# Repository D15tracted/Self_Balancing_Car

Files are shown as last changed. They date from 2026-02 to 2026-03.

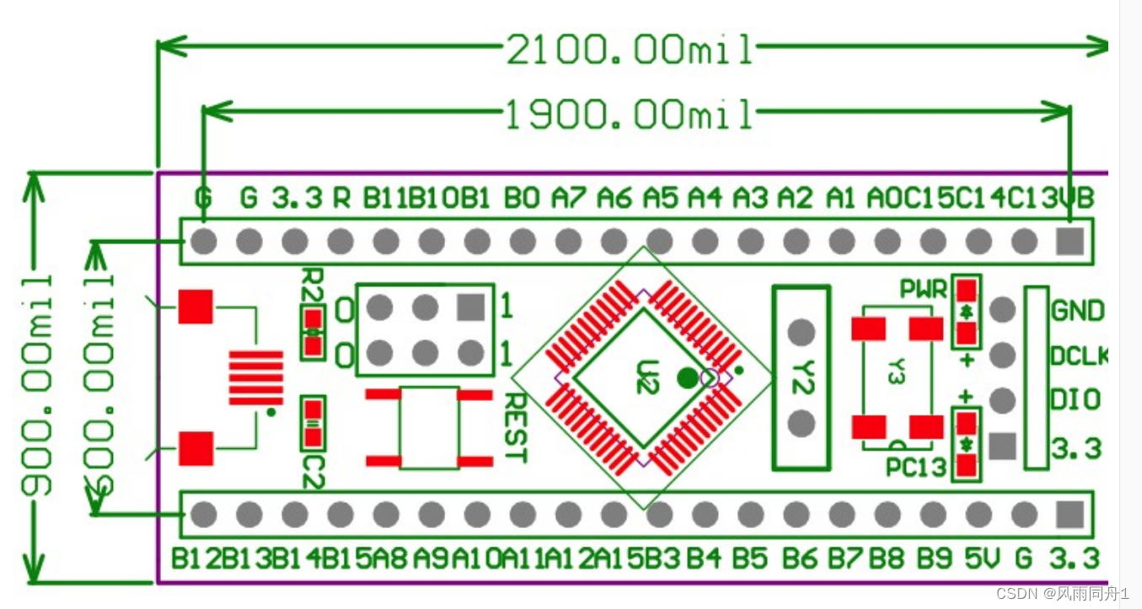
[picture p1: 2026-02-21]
Hardware/Datasheet/STM32F103C8T6_size.png

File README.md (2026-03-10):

# Self_Balancing_Car
This is a project based on tutorials from Bilibili, it have different mechanical stucture and controw board, it use a dm3519 brushless motor instead of a brush motor

related libaries: https://jiangxiekeji.com/download.html
                  https://gitee.com/kit-miao/damiao

Updates:
2026/3/10 implement HAL library

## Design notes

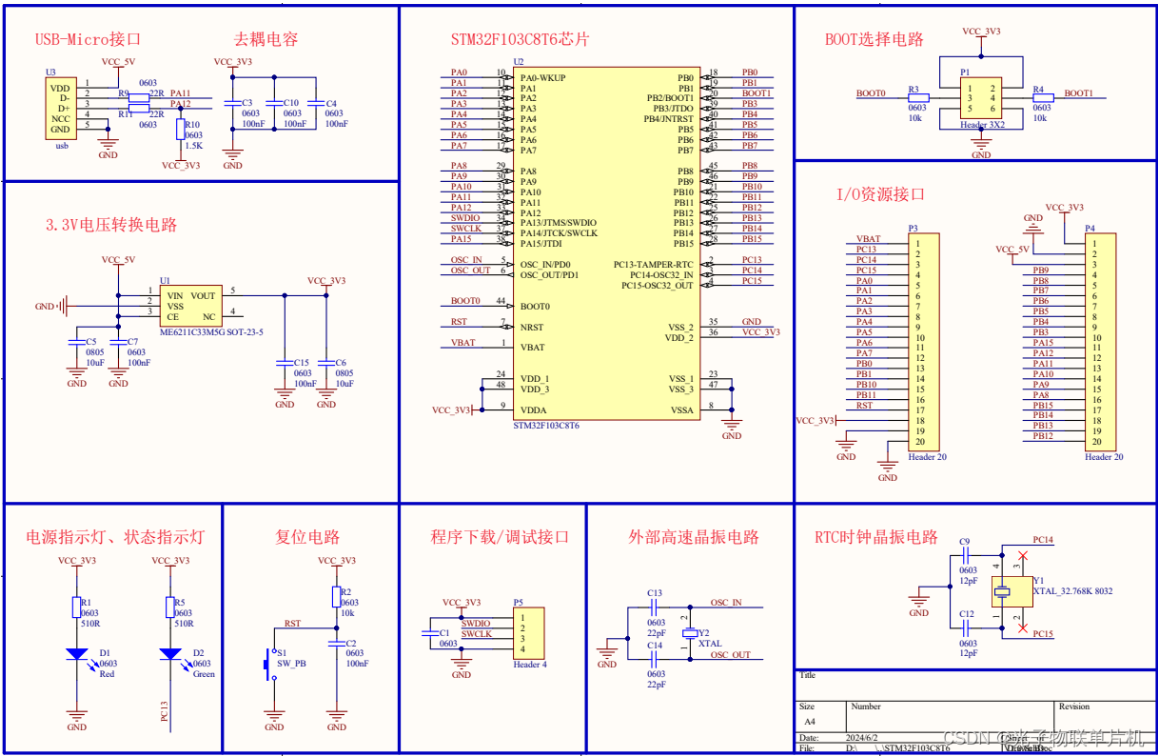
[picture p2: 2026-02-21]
Hardware/Datasheet/STM32F103C8T6_sch.png

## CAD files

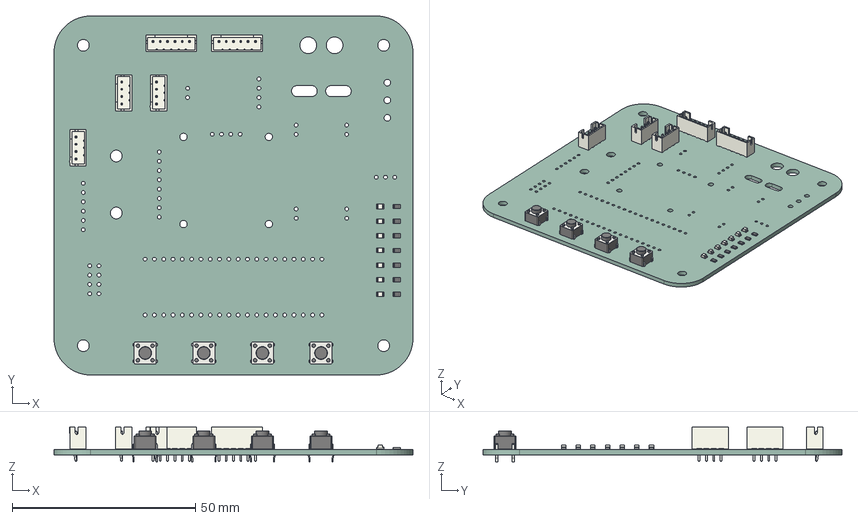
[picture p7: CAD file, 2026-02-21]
Hardware/Self_Balancing_Car.step
98.0 x 98.0 x 9.50 mm
R_0805_2012Metric x 7
LED_0805_2012Metric x 7
SW_PUSH_6mm_H5mm x 4
JST_PH_B6B-PH-K_1x06_P2.00mm_Vertical x 2
JST_PH_B4B-PH-K_1x04_P2.00mm_Vertical x 3
Self_Balancing_Car_PCB

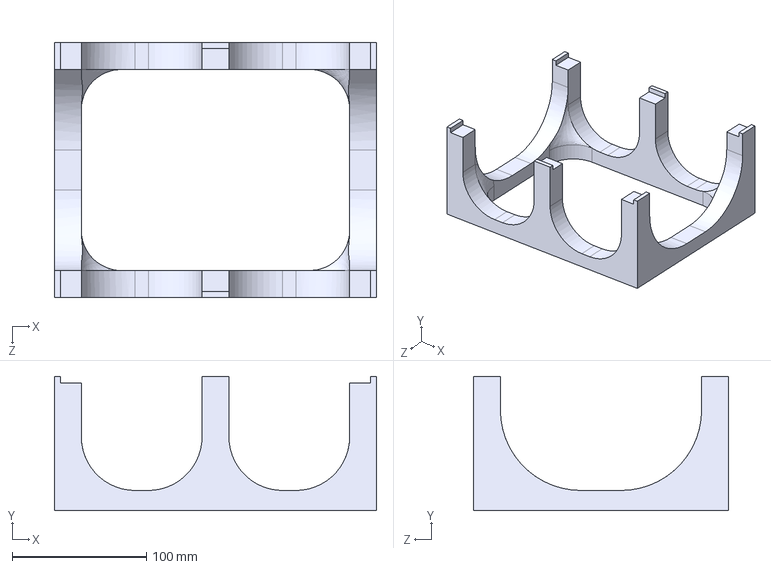
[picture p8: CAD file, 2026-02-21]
Mechanical/!Manufacture/3DP/Rack.STEP
240.0 x 100.0 x 190.0 mm

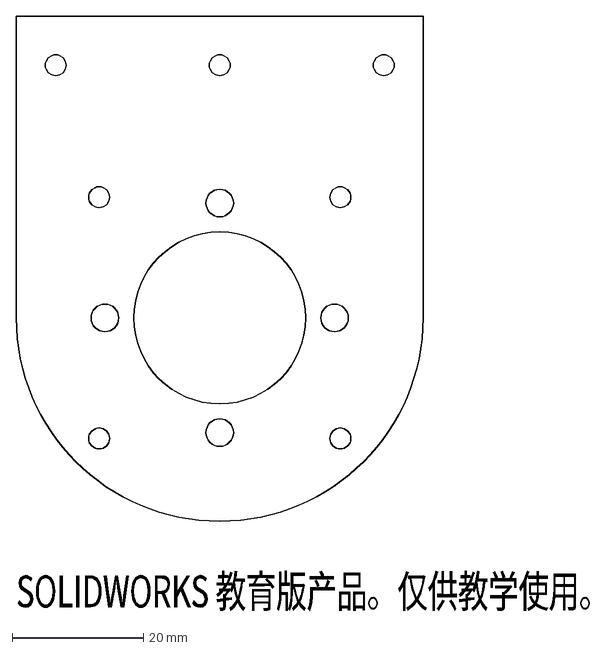
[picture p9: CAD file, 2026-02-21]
Mechanical/!Manufacture/CFP/SBC_CFP03.DXF
SOLIDWORKS 教育版产品。仅供教学使用。

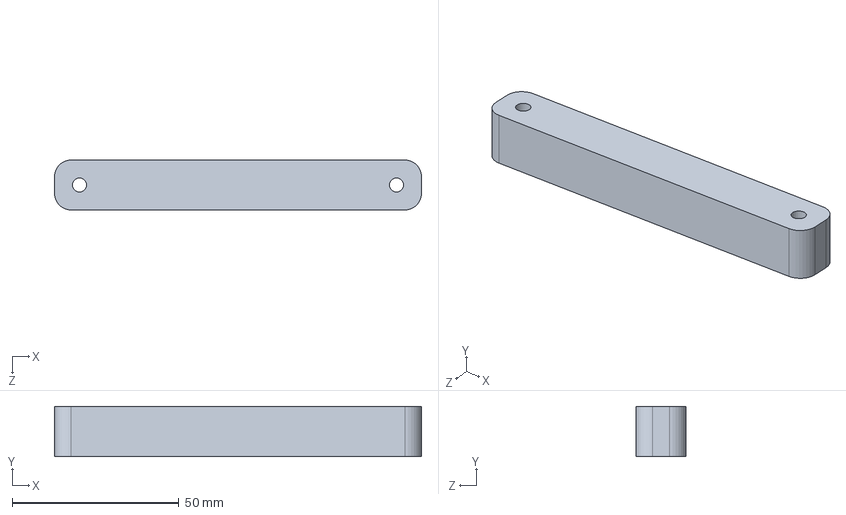
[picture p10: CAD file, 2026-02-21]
Mechanical/3DP/SBC_3DP05.SLDPRT
110.0 x 15.0 x 15.0 mm

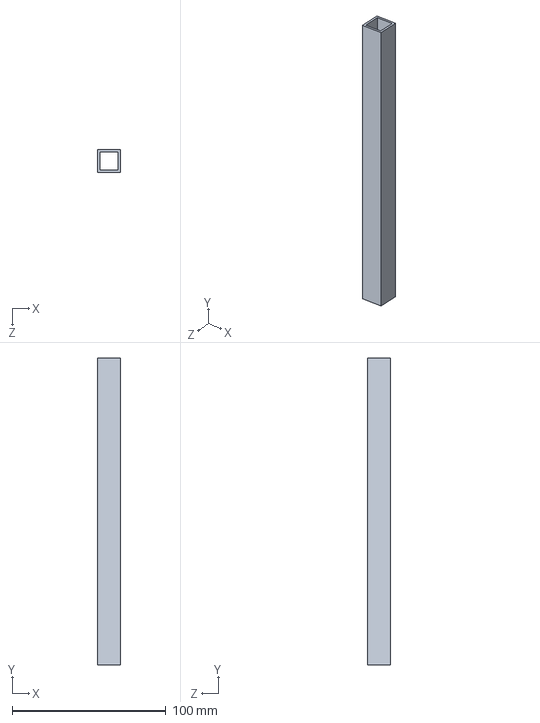
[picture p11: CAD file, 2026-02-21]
Mechanical/Altube/SBC_Altube01.SLDPRT
15.0 x 200.0 x 15.0 mm

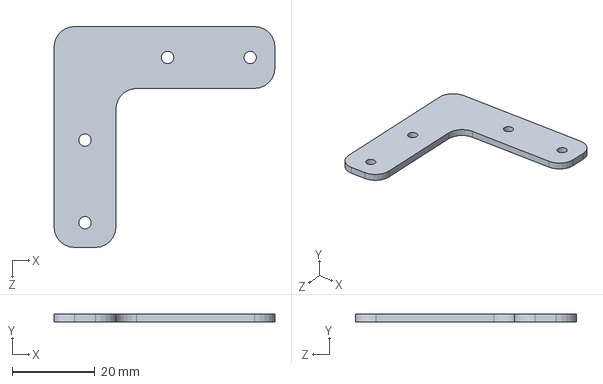
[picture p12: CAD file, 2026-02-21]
Mechanical/CFP/Template90LShape(15mm).SLDPRT
53.5 x 2.00 x 53.5 mm

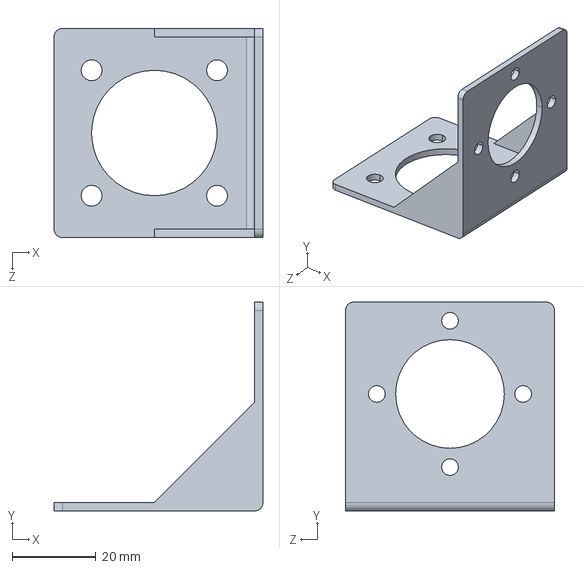
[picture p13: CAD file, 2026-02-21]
Mechanical/Misc/3508电机座.SLDPRT
50.0 x 50.0 x 50.0 mm

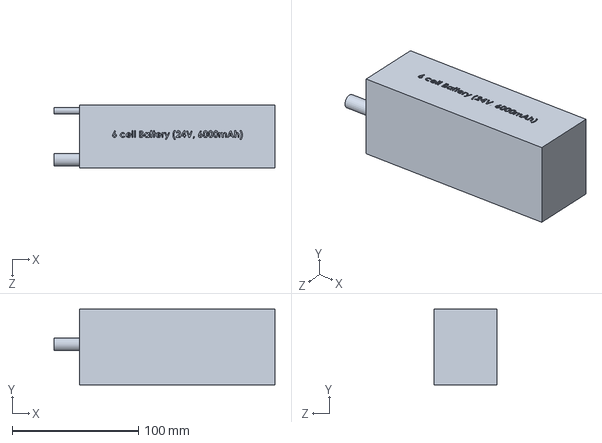
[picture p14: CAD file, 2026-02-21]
Hardware/6 cell battery (24V, 6000mAh).SLDPRT
175.0 x 60.0 x 50.0 mm

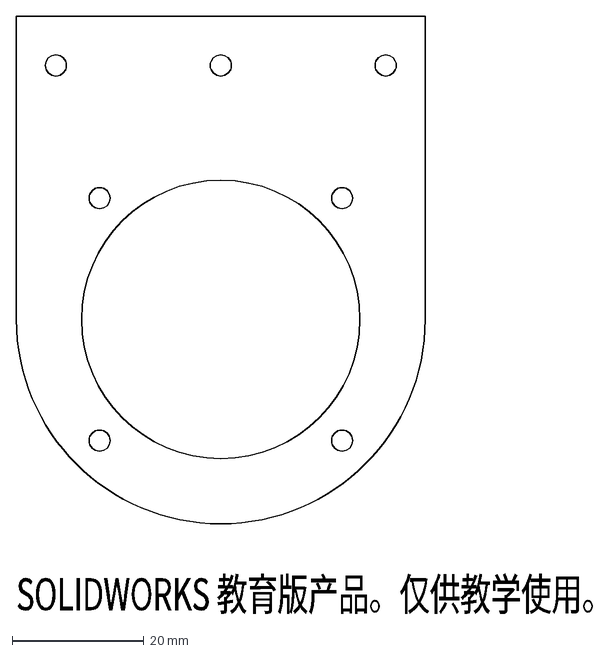
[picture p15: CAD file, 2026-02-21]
Mechanical/!Manufacture/CFP/SBC_CFP04.DXF
SOLIDWORKS 教育版产品。仅供教学使用。

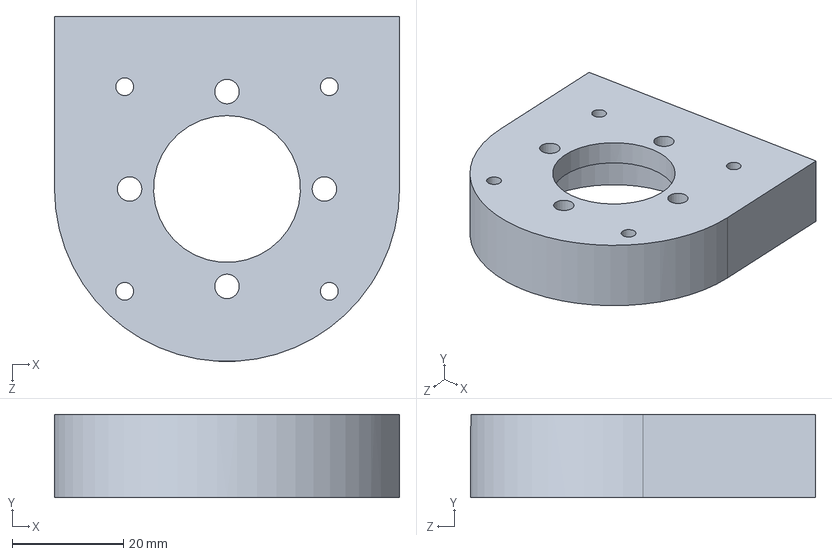
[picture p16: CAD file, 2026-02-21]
Mechanical/3DP/SBC_3DP01.SLDPRT
62.0 x 15.0 x 62.0 mm

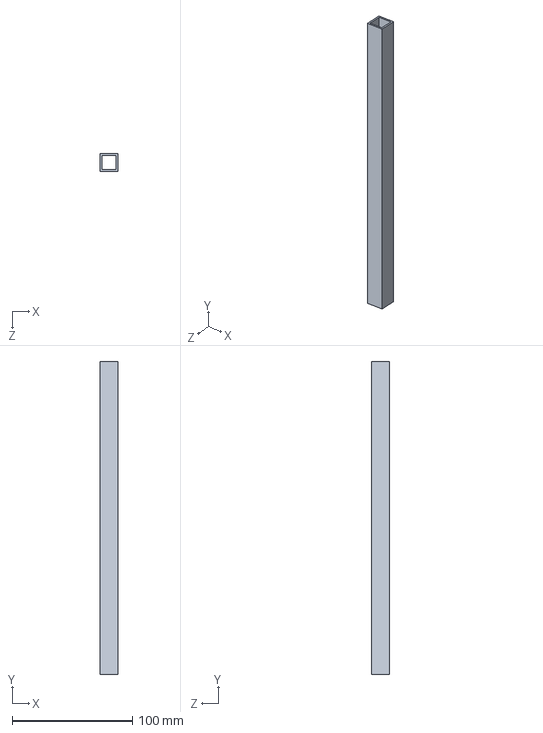
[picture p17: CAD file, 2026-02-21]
Mechanical/Altube/SBC_Altube02.SLDPRT
15.0 x 260.0 x 15.0 mm

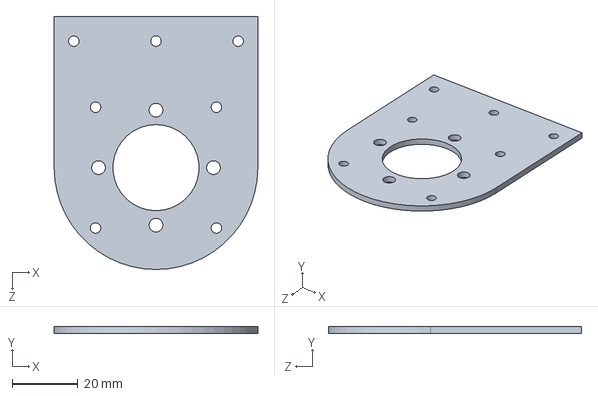
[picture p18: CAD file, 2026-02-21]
Mechanical/CFP/SBC_CFP03.SLDPRT
62.0 x 2.00 x 77.0 mm

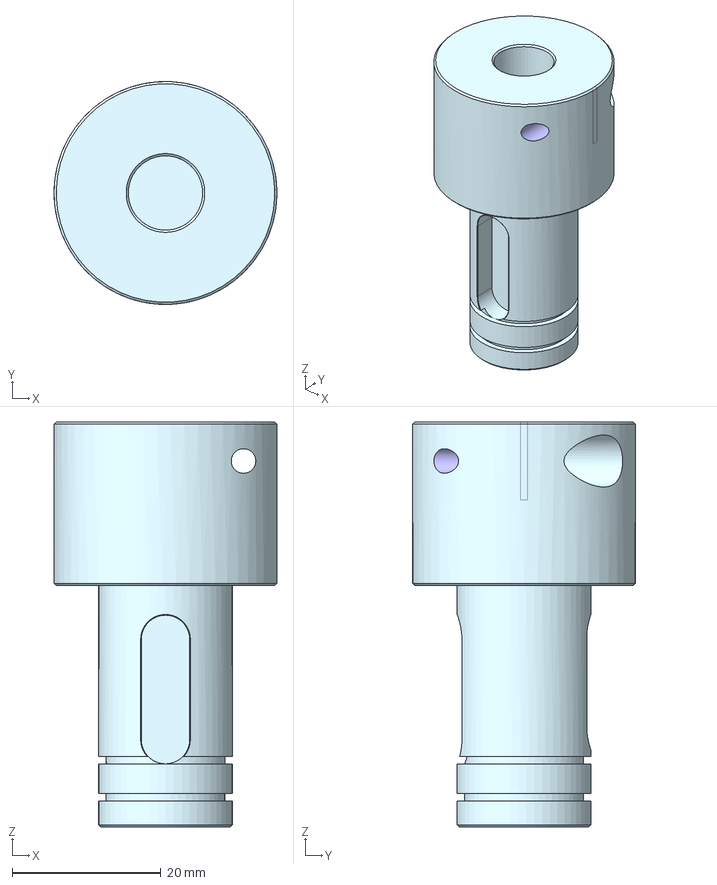
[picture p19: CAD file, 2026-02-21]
Mechanical/Misc/轴直径10mm-抱紧式联轴器-承重轮专用.stp
30.0 x 30.0 x 54.5 mm

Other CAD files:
Mechanical/Rack.SLDPRT
Mechanical/!Manufacture/3DP/SBC_3DP05.STEP
Mechanical/Hardware/SBC_board.SLDPRT
Hardware/SBC_board.SLDPRT
Hardware/3 cell battery (12V, 5200mAh).SLDPRT
Mechanical/!Manufacture/3DP/Rack.3mf
Mechanical/!Manufacture/3DP/SBC_3DP01.3mf
Mechanical/!Manufacture/3DP/SBC_3DP01.STEP
Mechanical/!Manufacture/3DP/SBC_3DP02.STEP
Mechanical/!Manufacture/3DP/SBC_3DP03.3mf
Mechanical/!Manufacture/3DP/SBC_3DP03.STEP
Mechanical/!Manufacture/3DP/SBC_3DP04.STEP
Mechanical/!Manufacture/3DP/SBC_3DP05.3mf
Mechanical/!Manufacture/Altube/SBC_Altube.SLDDRW
Mechanical/!Manufacture/CFP/SBC_CFP01.DXF
Mechanical/!Manufacture/CFP/SBC_CFP02.DXF
Mechanical/!Manufacture/CFP/SBC_CFP05.DXF
Mechanical/!Manufacture/CFP/Template90LShape(15mm).DXF
Mechanical/!Manufacture/CFP/Template90TShape(15mm).DXF
Mechanical/3DP/SBC_3DP02.SLDPRT
Mechanical/3DP/SBC_3DP03.SLDPRT
Mechanical/3DP/SBC_3DP04.SLDPRT
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

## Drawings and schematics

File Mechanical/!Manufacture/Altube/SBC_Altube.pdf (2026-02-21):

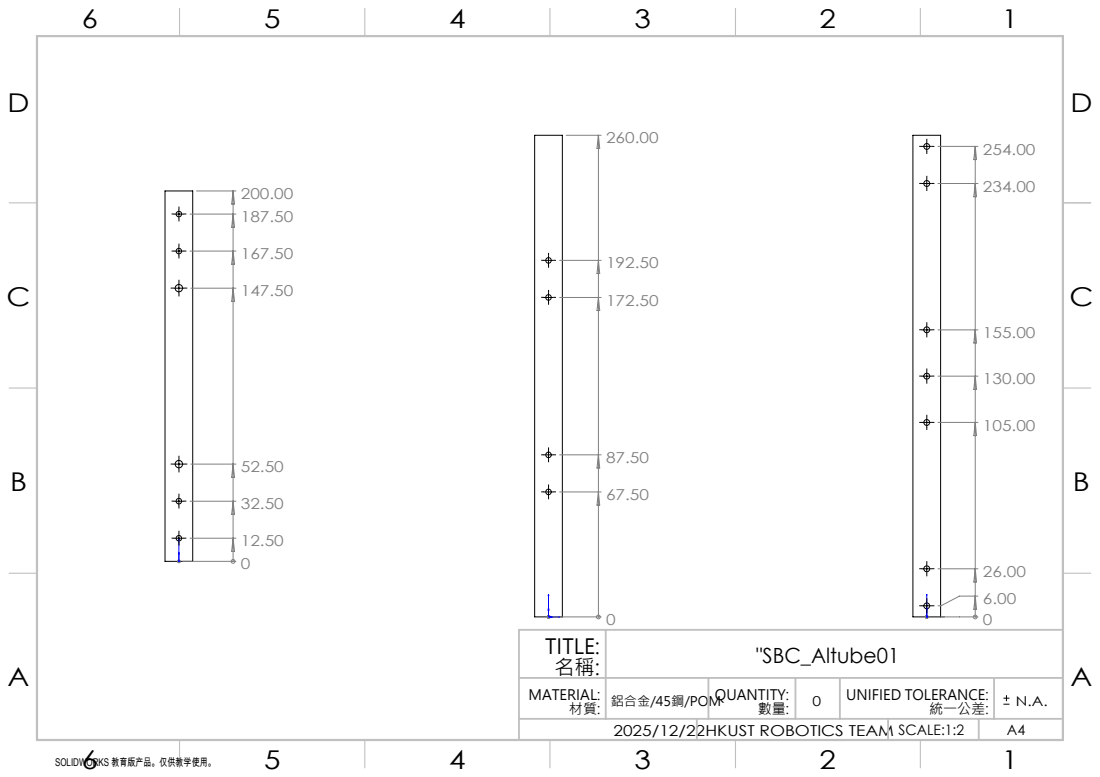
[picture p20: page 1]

TITLE: 名稱: | "SBC_Altube01

MATERIAL: 材質: | | QUANTITY: 數量: | 0 | UNIFIED TOLERANCE: 統一公差:

2025/12/22 | HKUST ROBOTICS TEAM | SCALE:1:2 | A4

SOLIDWORKS 教育版产品。仅供教学使用。

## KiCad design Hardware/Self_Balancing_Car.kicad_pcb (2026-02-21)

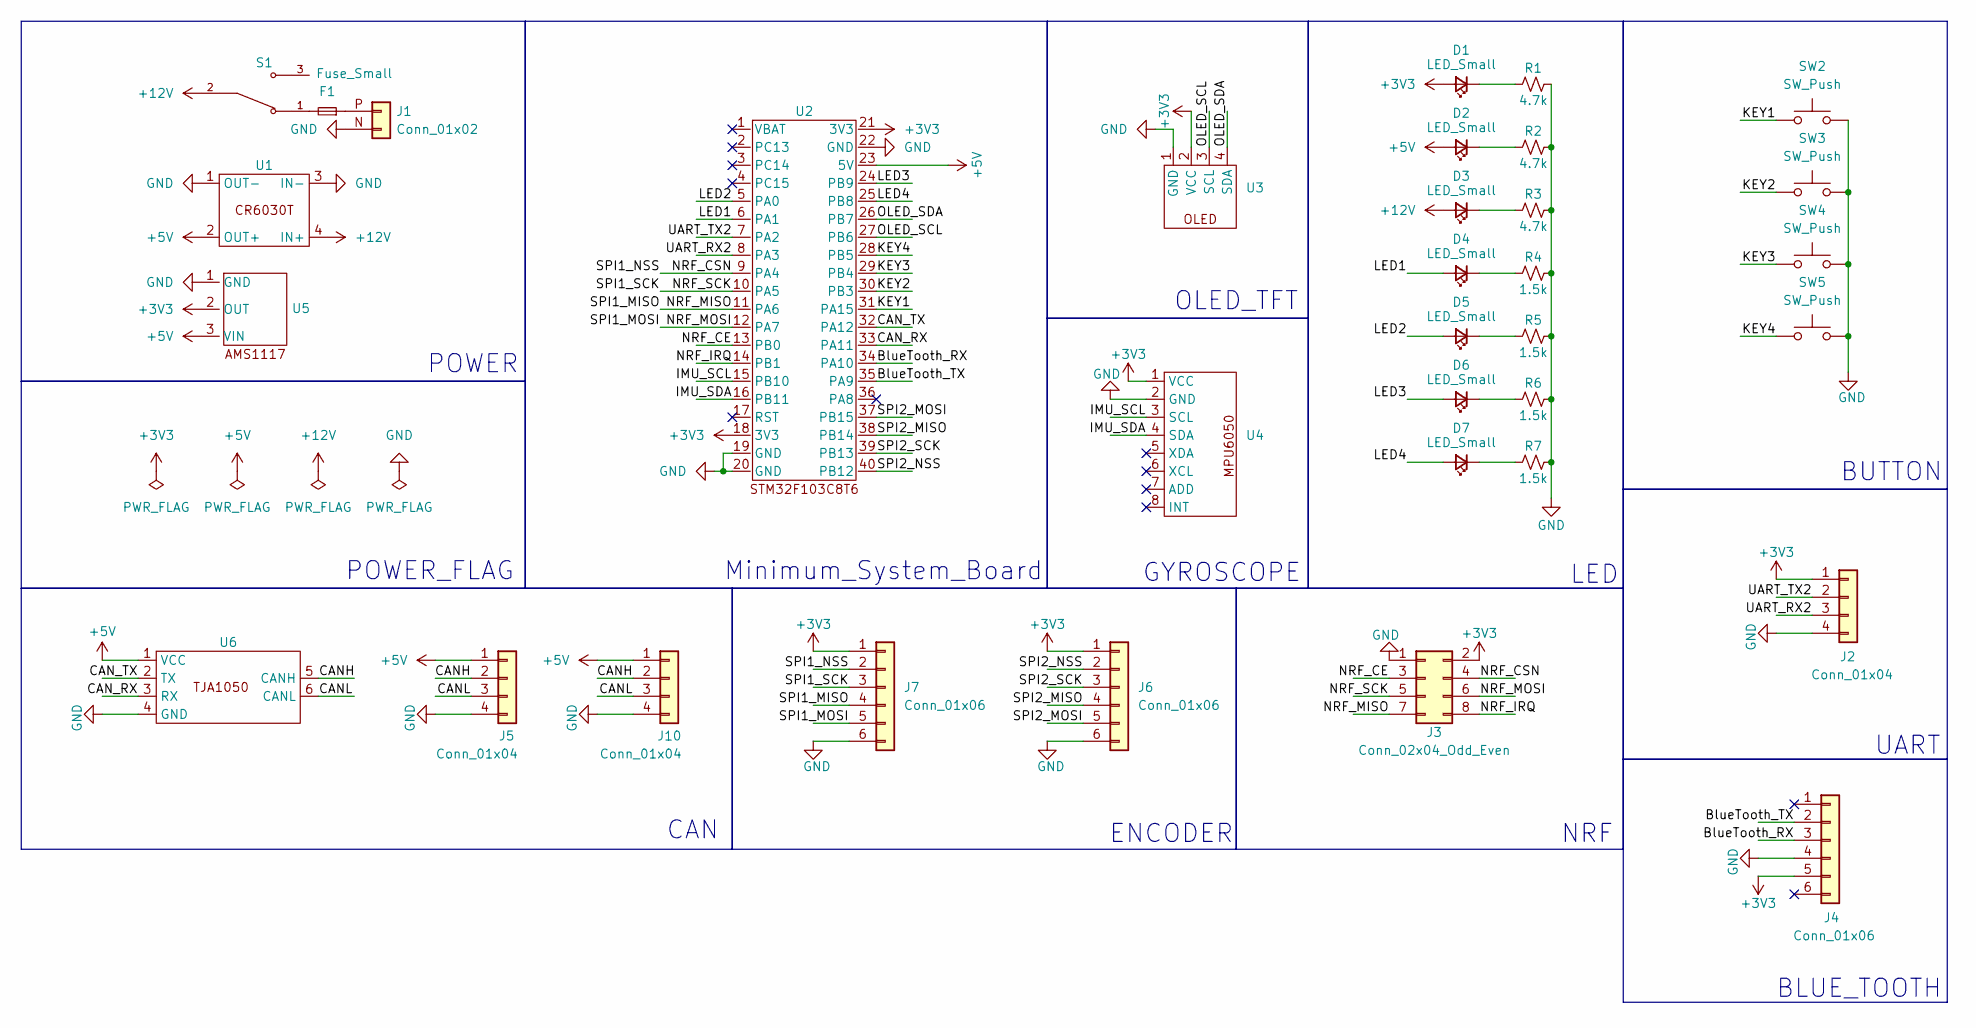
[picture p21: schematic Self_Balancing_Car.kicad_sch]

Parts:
D1, D2, D3, D4, D5, D6, D7: LED_Small; LED_0805_2012Metric
F1: Fuse_Small; Fuse_Blade_ATO_directSolder
J1: Conn_01x02; AMASS_XT60-M
J2, J5, J10: Conn_01x04; JST_PH_B4B-PH-K_1x04_P2.00mm_Vertical
J3: Conn_02x04_Odd_Even; NRF24L01
J4: Conn_01x06; BLUE_TOOTH
J6, J7: Conn_01x06; JST_PH_B6B-PH-K_1x06_P2.00mm_Vertical
R1, R2, R3: 4.7k; R_0805_2012Metric
R4, R5, R6, R7: 1.5k; R_0805_2012Metric
S1: SS12D10
SW2, SW3, SW4, SW5: SW_Push; KEY6x6
U1: CR6030T
U2: STM32F103C8T6_Minimum_System_Board
U3: OLED
U4: MPU6050
U5: AMS1117_Vertical
U6: TJA1050

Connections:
+3V3: D1.2 (A), J2.1, J3.2, J4.5, J6.1, J7.1, U2.18 (3V3), U2.21 (3V3), U3.2 (VCC), U4.1 (VCC), U5.2 (OUT)
+5V: D2.2 (A), J5.1, J10.1, U1.2 (OUT+), U2.23 (5V), U5.3 (VIN), U6.1 (VCC)
+12V: D3.2 (A), S1.2, U1.4 (IN+)
/BlueTooth_RX: J4.3, U2.34 (PA10)
/BlueTooth_TX: J4.2, U2.35 (PA9)
/CANH: J5.2, J10.2, U6.5 (CANH)
/CANL: J5.3, J10.3, U6.6 (CANL)
/CAN_RX: U2.33 (PA11), U6.3 (RX)
/CAN_TX: U2.32 (PA12), U6.2 (TX)
/IMU_SCL: U2.15 (PB10), U4.3 (SCL)
/IMU_SDA: U2.16 (PB11), U4.4 (SDA)
/KEY1: SW2.1, U2.31 (PA15)
/KEY2: SW3.1, U2.30 (PB3)
/KEY3: SW4.1, U2.29 (PB4)
/KEY4: SW5.1, U2.28 (PB5)
/LED1: D4.2 (A), U2.6 (PA1)
/LED2: D5.2 (A), U2.5 (PA0)
/LED3: D6.2 (A), U2.24 (PB9)
/LED4: D7.2 (A), U2.25 (PB8)
/NRF_CE: J3.3, U2.13 (PB0)
/NRF_CSN: J3.4, J7.2, U2.9 (PA4)
/NRF_IRQ: J3.8, U2.14 (PB1)
/NRF_MISO: J3.7, J7.4, U2.11 (PA6)
/NRF_MOSI: J3.6, J7.5, U2.12 (PA7)
/NRF_SCK: J3.5, J7.3, U2.10 (PA5)
/OLED_SCL: U2.27 (PB6), U3.3 (SCL)
/OLED_SDA: U2.26 (PB7), U3.4 (SDA)
/SPI2_MISO: J6.4, U2.38 (PB14)
/SPI2_MOSI: J6.5, U2.37 (PB15)
/SPI2_NSS: J6.2, U2.40 (PB12)
/SPI2_SCK: J6.3, U2.39 (PB13)
/UART_RX2: J2.3, U2.8 (PA3)
/UART_TX2: J2.2, U2.7 (PA2)
GND: J1.N (Pin_2), J2.4, J3.1, J4.4, J5.4, J6.6, J7.6, J10.4, R1.2, R2.2, R3.2, R4.2, R5.2, R6.2, R7.2, SW2.2, SW3.2, SW4.2, SW5.2, U1.1 (OUT-), U1.3 (IN-), U2.19 (GND), U2.20 (GND), U2.22 (GND), U3.1 (GND), U4.2 (GND), U5.1 (GND), U6.4 (GND)
unnamed: D1.1 (K), R1.1
unnamed: D2.1 (K), R2.1
unnamed: D3.1 (K), R3.1
unnamed: D4.1 (K), R4.1
unnamed: D5.1 (K), R5.1
unnamed: D6.1 (K), R6.1
unnamed: D7.1 (K), R7.1
unnamed: F1.2, S1.1
unnamed: F1.1, J1.P (Pin_1)

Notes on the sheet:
BUTTON
Minimum_System_Board
LED
ENCODER
POWER
NRF
GYROSCOPE
UART
POWER_FLAG
OLED_TFT
CAN
BLUE_TOOTH

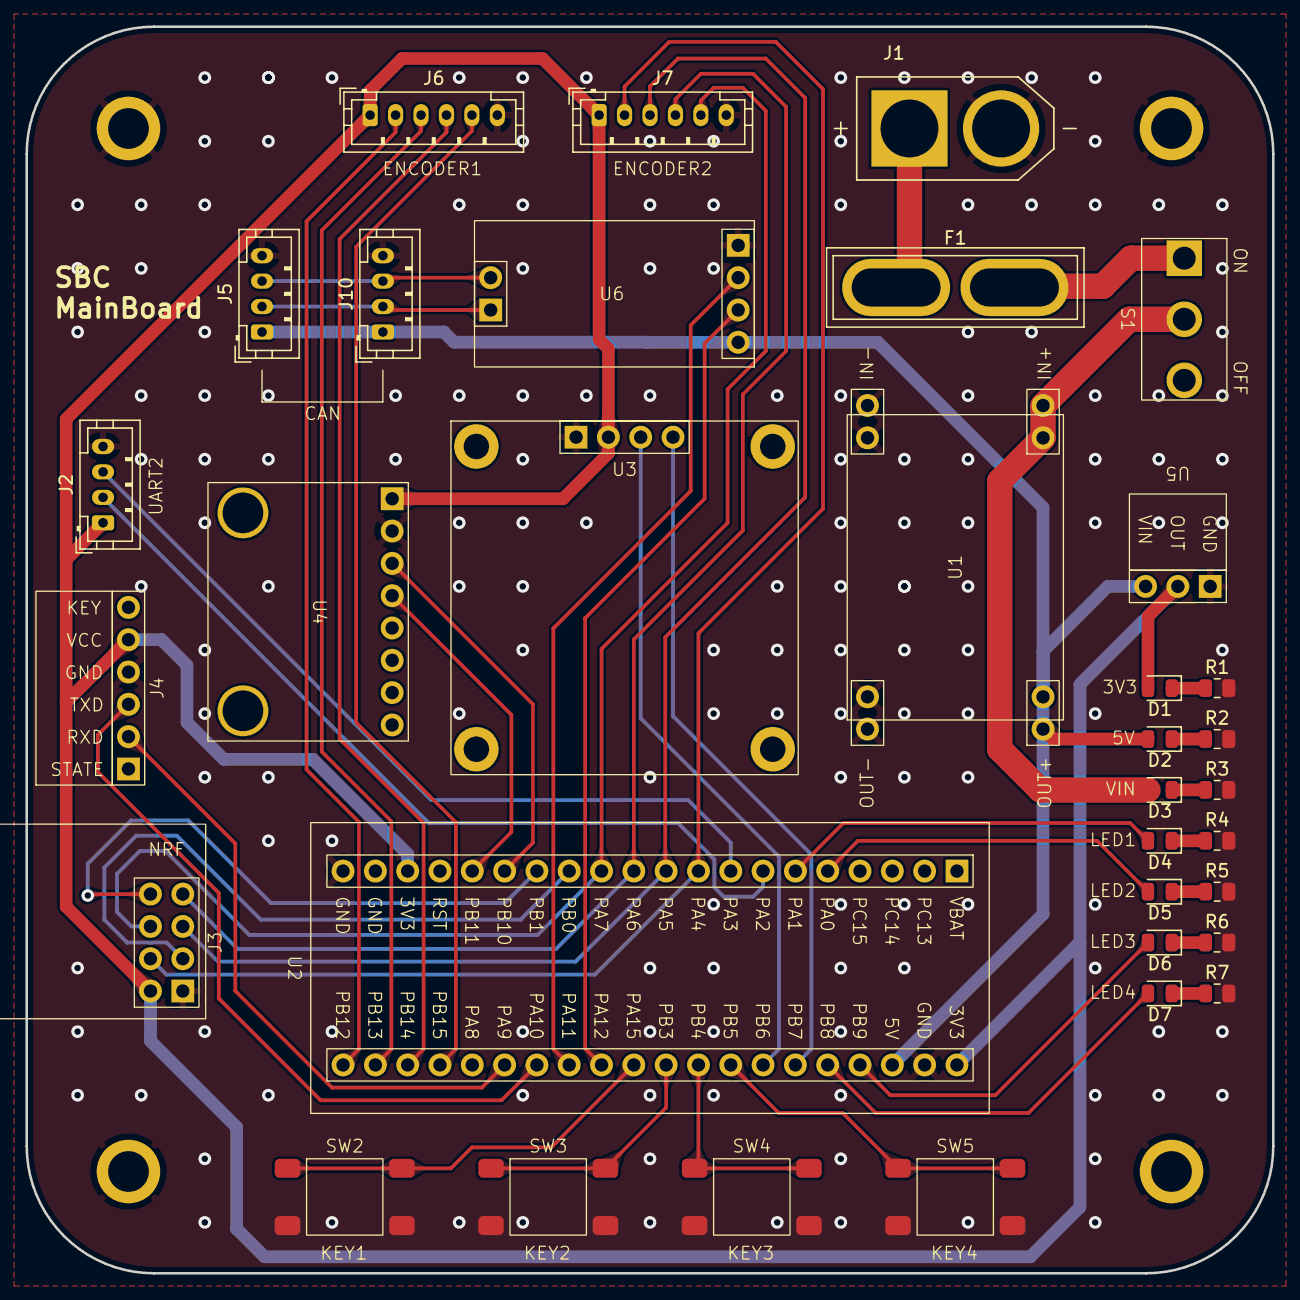
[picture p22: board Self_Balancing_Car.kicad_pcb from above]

Board: 2 copper layers, 98.0 x 98.0 mm, 34 parts (0 on the bottom side), 43 nets.

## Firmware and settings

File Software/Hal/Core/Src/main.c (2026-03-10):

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
/* Includes ------------------------------------------------------------------*/
#include "main.h"
#include "can.h"
#include "tim.h"
#include "usart.h"
#include "gpio.h"

/* USER CODE BEGIN Includes */
#include "OLED.h"
#include "MPU6050.h"
#include "Serial.h"
#include "Control.h"
#include "LED.h"
#include "KEY.h"
#include "MyCAN.h"
#include "dm_motor_ctrl.h"
#include "dm_motor_drv.h"
#include "PID.h"
#include <math.h>
#include <string.h>
#include <stdlib.h>

/* USER CODE END Includes */


/* USER CODE BEGIN PV */
uint8_t RunFlag;

int plotnum = 0;

float data[5] = {0,0,0,0,0};

float LmPos = 0;
float LmVel = 0;
float LmKp = 0;
float LmKd = 5;
float LmTor = 0;

float RmPos = 0;
float RmVel = 0;
float RmKp = 0;
float RmKd = 5;
float RmTor = 0;

float AngleActual2 = 0;

float SpeedActual2 = 0;

float TurnActual2 = 0;

float LeftSpeed1 = 0;

float RightSpeed1 = 0;

motor_t *m1;
motor_t *m2;

float AveVel, DifVel;

float LeftSpeed, RightSpeed;
float LeftSpeedFiltered, RightSpeedFiltered;
float AveSpeed;

uint32_t RxID;
uint8_t RxLength;
uint8_t RxData[8];

int16_t AX, AY, AZ, GX, GY, GZ;
uint8_t TimerErrorFlag;
uint16_t TimerCount;

float AngleAcc;
float AngleGyro;
float Angle;

PID_t AnglePID = {
	.Kp = 0.2, //0.2
	.Ki = 0.03,  //0.03
	.Kd = 0.1,  //0.1
	
	.OutMax = 100,
	.OutMin = -100,
	
	.OutOffset = 0,
	
	.ErrorDecayFactor = 1,
	.ErrorIntMax = 400,
	.ErrorIntMin = -400,
};

PID_t SpeedPID = {
	.Kp = 0.8,  //0.8
	.Ki = 0.1,  //0.1
	.Kd = 0.5,  //0.5
	
	.OutMax = 7,
	.OutMin = -7,
	
	.ErrorDecayFactor = 3,
	.ErrorIntMax = 50,
	.ErrorIntMin = -50,
};

static uint16_t Count0 = 0, Count1 = 0, Count2 = 0;
/* USER CODE END PV */

void SystemClock_Config(void);
/**
  * @brief  The application entry point.
  * @retval int
  */
int main(void)
{

  /* MCU Configuration--------------------------------------------------------*/

  /* Reset of all peripherals, Initializes the Flash interface and the Systick. */
  HAL_Init();

  /* USER CODE BEGIN Init */
	__HAL_AFIO_REMAP_SWJ_NOJTAG();
  /* USER CODE END Init */

  /* Configure the system clock */
  SystemClock_Config();

  /* Initialize all configured peripherals */
  MX_GPIO_Init();
  MX_CAN_Init();
  MX_USART1_UART_Init();
  MX_TIM1_Init();
  /* USER CODE BEGIN 2 */
	OLED_Init();
	MPU6050_Init();
	Serial_Init();
	MyCAN_Init();
	dm_motor_init();
	HAL_TIM_Base_Start_IT(&htim1);
	
	m1 = &motor[Motor1];
	m1->id = 0x01;
	m1->ctrl.mode = mit_mode;
	m1->para.pos = 0;
	m1->para.vel = 0;
	m1->para.tor = 0;
	
	m2 = &motor[Motor2];
	m2->id = 0x02;
	m2->ctrl.mode = mit_mode;
	m2->para.pos = 0;
	m2->para.vel = 0;
	m2->para.tor = 0;
  /* USER CODE END 2 */

  /* Infinite loop */
  /* USER CODE BEGIN WHILE */
  while (1)
  {
		if (RunFlag) {
		dm_motor_enable(m1);
		dm_motor_enable(m2);
		} 
		else {
		dm_motor_disable(m1);
		dm_motor_disable(m2);
		}
		
		if (RunFlag) {LED1_ON();} else {LED1_OFF();}
		
		if (Key_Check(KEY_1, KEY_DOWN))
		{
			if (RunFlag == 0)
			{
				PID_Init(&AnglePID);
				PID_Init(&SpeedPID);
				RunFlag = 1;
			}
			else
			{
				RunFlag = 0;
			}
		}
		
		OLED_Clear();
		
		if (Serial_RxFlag == 1){
			Control_Rx(data);
		}
		
		if(data[0] == 2){
				SpeedPID.Target = data[2] / 20.0;
				DifVel = -data[3] / 50.0;
		}
		
		if(data[0] == 2){
			if(fabsf(data[1]) > 95 || fabsf(data[4]) > 95){
				RunFlag = 0;
			}
		}
		
		if(data[0] == 3) {plotnum = data[1];}
		
		if(plotnum != 0){
			if(plotnum == 1){
				printf("[plot,%f,%f]", m1->para.pos, m2->para.pos);
			}
			if(plotnum == 2){
				printf("[plot,%f,%f]", m1->para.vel, m2->para.vel);
			}
			if(plotnum == 3){
				printf("[plot,%f,%f]", m1->para.tor, m2->para.tor);
			}
			if(plotnum == 4){
				printf("[plot,%f,%f,%f]", AngleAcc, AngleGyro, Angle);
			}
			if(plotnum == 5){
				printf("[plot,%f,%f,%f,%f,%f]", AnglePID.Kp * AnglePID.Error0, AnglePID.Ki * AnglePID.ErrorInt, AnglePID.Kd * AngleActual2, AnglePID.Target, AnglePID.Actual);
			}
			if(plotnum == 6){
				printf("[plot,%f,%f,%f,%f,%f]", SpeedPID.Kp * SpeedPID.Error0, SpeedPID.Ki * SpeedPID.ErrorInt, SpeedPID.Kd * SpeedActual2, SpeedPID.Target, SpeedPID.Actual);
			}
		}
		
		OLED_Printf(0, 0, OLED_6X8, "P:%05.2fr", m1->para.pos);
		OLED_Printf(0, 8, OLED_6X8, "V:%05.2fr/s", m1->para.vel);
		OLED_Printf(0, 16, OLED_6X8, "T:%05.2fNm", m1->para.tor);
		
		OLED_Printf(0, 32, OLED_6X8, "P:%05.2fr", m2->para.pos);
		OLED_Printf(0, 40, OLED_6X8, "V:%05.2fr/s", m2->para.vel);
		OLED_Printf(0, 48, OLED_6X8, "T:%05.2fNm", m2->para.tor);
		
		OLED_Printf(64, 0, OLED_6X8, "Aa:%05.2f", AngleAcc);
		OLED_Printf(64, 8, OLED_6X8, "Ag:%05.2f", AngleGyro);
		OLED_Printf(64, 16, OLED_6X8, "Af:%05.2f", Angle);
		
		OLED_Printf(64, 32, OLED_6X8, "%05d", AX);
		OLED_Printf(64, 40, OLED_6X8, "%05d",	AY);
		OLED_Printf(64, 48, OLED_6X8, "%05d", AZ);
		OLED_Printf(96, 32, OLED_6X8, "%05d", GX);
		OLED_Printf(96, 40, OLED_6X8, "%05d", GY);
		OLED_Printf(96, 48, OLED_6X8, "%05d", GZ);
		
		OLED_Printf(0, 56, OLED_6X8, "%01d", Serial_RxFlag);
		OLED_Printf(64, 56, OLED_6X8, "%02.2f", SpeedPID.Target);
		OLED_Printf(96, 56, OLED_6X8, "%02.2f", DifVel);

		OLED_Update();
    /* USER CODE END WHILE */

    /* USER CODE BEGIN 3 */
  }
  /* USER CODE END 3 */
}

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
/* USER CODE BEGIN 4 */
void HAL_TIM_PeriodElapsedCallback(TIM_HandleTypeDef *htim)
{
    if (htim->Instance == TIM1)
    {
        // 按键扫描（若 Key 模块依赖定时器）
        Key_Tick();   // 需确认 Key 模块是否已移植

        // 串口接收超时检测（Count2 逻辑）
        Count2++;
        if (Serial_RxFlag == 1) {
            Count2 = 0;
        }
        if (Count2 >= 500) {
            Count2 = 0;
            data[0] = 0; data[1] = 0; data[2] = 0; data[3] = 0; data[4] = 0;
            SpeedPID.Target = 0;
            DifVel = 0;
        }

        // 每 10ms 执行一次（假设定时器周期 1ms）
        Count0++;
        if (Count0 >= 10) {
            Count0 = 0;

            // 读取 MPU6050
            MPU6050_GetData(&AX, &AY, &AZ, &GX, &GY, &GZ);

            // 数据校准（根据原代码）
            GY = -GY;
            GY -= 114;
            AX = -AX;
            AZ = -AZ;

            // 角度计算
            AngleAcc = atan2(AX, AZ) / 3.14159f * 180.0f;
            AngleAcc += 3.55f;
            AngleGyro = Angle + (GY / 32768.0f * 2000.0f * 0.01f);
            float Alpha = 0.003f;
            Angle = Alpha * AngleAcc + (1.0f - Alpha) * AngleGyro;

            // 角度超限保护
            if (Angle > 15.0f || Angle < -15.0f) {
                RunFlag = 0;
            }

            // 电机控制输出
            if (RunFlag) {
                AnglePID.Actual = Angle;
                AngleActual2 = AnglePID.Actual - AnglePID.Actual1;
                PID_Update(&AnglePID);
                AveVel = -AnglePID.Out;

                LmVel = AveVel + DifVel / 2.0f;
                RmVel = AveVel - DifVel / 2.0f;

                // 限幅
                if (LmVel > 10.0f) LmVel = 10.0f;
                else if (LmVel < -10.0f) LmVel = -10.0f;
                if (RmVel > 10.0f) RmVel = 10.0f;
                else if (RmVel < -10.0f) RmVel = -10.0f;

                // 发送 MIT 控制命令
                mit_ctrl(m1, 0x01, LmPos, LmVel, LmKp, LmKd, LmTor);
                mit_ctrl(m2, 0x02, RmPos, -RmVel, RmKp, RmKd, RmTor);
            } else {
                // 停机
                mit_ctrl(m1, 0x01, 0, 0, 0, 0, 0);
                mit_ctrl(m2, 0x02, 0, 0, 0, 0, 0);
            }
        }

        // 每 10ms 读取电机反馈
        Count1++;
        if (Count1 >= 10) {
            Count1 = 0;

            // 发送读取命令
            read_motor_ctrl_fbdata(0x01);
						MyCAN_Receive(&RxID, &RxLength, RxData);
						dm_motor_fbdata(m1, RxData);
		
						read_motor_ctrl_fbdata(0x02);
						MyCAN_Receive(&RxID, &RxLength, RxData);
						dm_motor_fbdata(m2, RxData);

            // 速度滤波
            float LeftSpeedRaw = m1->para.vel;
            float RightSpeedRaw = m2->para.vel;
					
            float Beta = 0.1f;
            LeftSpeedFiltered = Beta * LeftSpeedRaw + (1.0f - Beta) * LeftSpeedFiltered;
            RightSpeedFiltered = Beta * RightSpeedRaw + (1.0f - Beta) * RightSpeedFiltered;
            
						LeftSpeed = LeftSpeedFiltered;
            RightSpeed = RightSpeedFiltered;

            AveSpeed = (LeftSpeed - RightSpeed) / 2.0f;

            if (RunFlag) {
                SpeedPID.Actual = AveSpeed;
                SpeedActual2 = SpeedPID.Actual - SpeedPID.Actual1;
                PID_Update(&SpeedPID);
                AnglePID.Target = -SpeedPID.Out;

                if (AveSpeed * AnglePID.Target < 0) {
                    if (AnglePID.Target > 5.0f) AnglePID.Target = 5.0f;
                    if (AnglePID.Target < -5.0f) AnglePID.Target = -5.0f;
                }
            }
        }

        // 可选：记录定时器计数
        TimerCount = __HAL_TIM_GET_COUNTER(&htim1);
    }
}

void HAL_CAN_RxFifo0MsgPendingCallback(CAN_HandleTypeDef *hcan)
{
    // 调用电机驱动接收处理函数
    Motor_CAN_RxHandler();
}
/* USER CODE END 4 */
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


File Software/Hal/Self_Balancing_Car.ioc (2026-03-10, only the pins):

Mcu.UserName=STM32F103C8Tx
PA0-WKUP.GPIO_Label=LED2
PA0-WKUP.Signal=GPIO_Output
PA1.GPIO_Label=LED1
PA1.Signal=GPIO_Output
PA10.Signal=USART1_RX
PA11.Signal=CAN_RX
PA12.Signal=CAN_TX
PA13.Signal=SYS_JTMS-SWDIO
PA14.Signal=SYS_JTCK-SWCLK
PA15.GPIO_Label=KEY1
PA15.Signal=GPIO_Input
PA9.Signal=USART1_TX
PB10.Signal=GPIO_Output
PB11.Signal=GPIO_Output
PB3.GPIO_Label=KEY2
PB3.Signal=GPIO_Input
PB4.GPIO_Label=KEY3
PB4.Signal=GPIO_Input
PB5.GPIO_Label=KEY4
PB5.Signal=GPIO_Input
PB6.Signal=GPIO_Output
PB7.Signal=GPIO_Output
PB8.GPIO_Label=LED4
PB8.Signal=GPIO_Output
PB9.GPIO_Label=LED3
PB9.Signal=GPIO_Output
PC14-OSC32_IN.Signal=RCC_OSC32_IN
PC15-OSC32_OUT.Signal=RCC_OSC32_OUT
PD0-OSC_IN.Signal=RCC_OSC_IN
PD1-OSC_OUT.Signal=RCC_OSC_OUT

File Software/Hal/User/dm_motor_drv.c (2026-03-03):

#include "dm_motor_drv.h"
#include <string.h>

// DM3519 四电机电流控制（ID 为 0x280 等，根据实际调整）
void dm3519_current_set(uint16_t id, float m1_cur_set, float m2_cur_set,
                        float m3_cur_set, float m4_cur_set)
{
    uint8_t data[8];
    int16_t m1_cur_tmp = (int16_t)(m1_cur_set * (16384.0f / 20.0f));
    int16_t m2_cur_tmp = (int16_t)(m2_cur_set * (16384.0f / 20.0f));
    int16_t m3_cur_tmp = (int16_t)(m3_cur_set * (16384.0f / 20.0f));
    int16_t m4_cur_tmp = (int16_t)(m4_cur_set * (16384.0f / 20.0f));

    data[0] = m1_cur_tmp >> 8;
    data[1] = m1_cur_tmp & 0xFF;
    data[2] = m2_cur_tmp >> 8;
    data[3] = m2_cur_tmp & 0xFF;
    data[4] = m3_cur_tmp >> 8;
    data[5] = m3_cur_tmp & 0xFF;
    data[6] = m4_cur_tmp >> 8;
    data[7] = m4_cur_tmp & 0xFF;

    MyCAN_Transmit(id, 8, data);
}

// DM3519 反馈数据处理（8字节数据）
void dm3519_fbdata(motor_t *motor, uint8_t *rx_data)
{
    int16_t pos_int16 = (rx_data[0] << 8) | rx_data[1];
    int16_t spd_int16 = (rx_data[2] << 8) | rx_data[3];
    int16_t cur_int16 = (rx_data[4] << 8) | rx_data[5];

    motor->para.pos  = (float)pos_int16 / 8192.0f * 360.0f;   // 圈数 -> 度
    motor->para.vel  = (float)spd_int16;                      // 速度（单位取决于电机）
    motor->para.cur  = (float)cur_int16 / (16384.0f / 20.0f); // 电流（A）
    motor->para.Tcoil = (float)rx_data[6];
    motor->para.Tmos  = (float)rx_data[7];
}

// 浮点数转无符号整数（用于MIT模式打包）
int float_to_uint(float x_float, float x_min, float x_max, int bits)
{
    float span = x_max - x_min;
    float offset = x_min;
    return (int)((x_float - offset) * ((float)((1 << bits) - 1)) / span);
}

// 无符号整数转浮点数（用于MIT模式解包）
float uint_to_float(int x_int, float x_min, float x_max, int bits)
{
    float span = x_max - x_min;
    float offset = x_min;
    return (float)x_int * span / ((float)((1 << bits) - 1)) + offset;
}

// 启用电机模式
void enable_motor_mode(uint16_t motor_id, uint16_t mode_id)
{
    uint8_t data[8] = {0xFF, 0xFF, 0xFF, 0xFF, 0xFF, 0xFF, 0xFF, 0xFC};
    uint16_t id = motor_id + mode_id;
    MyCAN_Transmit(id, 8, data);
}

// 禁用电机模式
void disable_motor_mode(uint16_t motor_id, uint16_t mode_id)
{
    uint8_t data[8] = {0xFF, 0xFF, 0xFF, 0xFF, 0xFF, 0xFF, 0xFF, 0xFD};
    uint16_t id = motor_id + mode_id;
    MyCAN_Transmit(id, 8, data);
}

// 保存当前位置为零点
void save_pos_zero(uint16_t motor_id, uint16_t mode_id)
{
    uint8_t data[8] = {0xFF, 0xFF, 0xFF, 0xFF, 0xFF, 0xFF, 0xFF, 0xFE};
    uint16_t id = motor_id + mode_id;
    MyCAN_Transmit(id, 8, data);
}

// 清除错误
void clear_err(uint16_t motor_id, uint16_t mode_id)
{
    uint8_t data[8] = {0xFF, 0xFF, 0xFF, 0xFF, 0xFF, 0xFF, 0xFF, 0xFB};
    uint16_t id = motor_id + mode_id;
    MyCAN_Transmit(id, 8, data);
}

// MIT 模式控制
void mit_ctrl(motor_t *motor, uint16_t motor_id, float pos, float vel,
              float kp, float kd, float tor)
{
    uint8_t data[8];
    uint16_t pos_tmp, vel_tmp, kp_tmp, kd_tmp, tor_tmp;
    uint16_t id = motor_id + MIT_MODE;

    pos_tmp = float_to_uint(pos, -motor->tmp.PMAX, motor->tmp.PMAX, 16);
    vel_tmp = float_to_uint(vel, -motor->tmp.VMAX, motor->tmp.VMAX, 12);
    tor_tmp = float_to_uint(tor, -motor->tmp.TMAX, motor->tmp.TMAX, 12);
    kp_tmp  = float_to_uint(kp,  KP_MIN, KP_MAX, 12);
    kd_tmp  = float_to_uint(kd,  KD_MIN, KD_MAX, 12);

    data[0] = pos_tmp >> 8;
    data[1] = pos_tmp & 0xFF;
    data[2] = vel_tmp >> 4;
    data[3] = ((vel_tmp & 0x0F) << 4) | (kp_tmp >> 8);
    data[4] = kp_tmp & 0xFF;
    data[5] = kd_tmp >> 4;
    data[6] = ((kd_tmp & 0x0F) << 4) | (tor_tmp >> 8);
    data[7] = tor_tmp & 0xFF;

    MyCAN_Transmit(id, 8, data);
}

// 位置模式控制（发送 float 位置和速度）
void pos_ctrl(uint16_t motor_id, float pos, float vel)
{
    uint16_t id = motor_id + POS_MODE;
    uint8_t *pbuf = (uint8_t*)&pos;
    uint8_t *vbuf = (uint8_t*)&vel;
    uint8_t data[8];

    data[0] = pbuf[0];
    data[1] = pbuf[1];
    data[2] = pbuf[2];
    data[3] = pbuf[3];
    data[4] = vbuf[0];
    data[5] = vbuf[1];
    data[6] = vbuf[2];
    data[7] = vbuf[3];

    MyCAN_Transmit(id, 8, data);
}

// 速度模式控制（发送 float 速度）
void spd_ctrl(uint16_t motor_id, float vel)
{
    uint16_t id = motor_id + SPD_MODE;
    uint8_t *vbuf = (uint8_t*)&vel;
    uint8_t data[4];

    data[0] = vbuf[0];
    data[1] = vbuf[1];
    data[2] = vbuf[2];
    data[3] = vbuf[3];

    MyCAN_Transmit(id, 4, data);
}

// 混控模式（位置 + 速度 + 电流）
void psi_ctrl(uint16_t motor_id, float pos, float vel, float cur)
{
    uint16_t id = motor_id + PSI_MODE;
    uint8_t *pbuf = (uint8_t*)&pos;
    uint16_t u16_vel = (uint16_t)(vel * 100);
    uint16_t u16_cur = (uint16_t)(cur * 10000);
    uint8_t *vbuf = (uint8_t*)&u16_vel;
    uint8_t *ibuf = (uint8_t*)&u16_cur;
    uint8_t data[8];

    data[0] = pbuf[0];
    data[1] = pbuf[1];
    data[2] = pbuf[2];
    data[3] = pbuf[3];
    data[4] = vbuf[0];
    data[5] = vbuf[1];
    data[6] = ibuf[0];
    data[7] = ibuf[1];

    MyCAN_Transmit(id, 8, data);
}

// 电机使能（根据当前设定的模式）
void dm_motor_enable(motor_t *motor)
{
    switch (motor->ctrl.mode) {
        case mit_mode:
            enable_motor_mode(motor->id, MIT_MODE);
            break;
        case pos_mode:
            enable_motor_mode(motor->id, POS_MODE);
            break;
        case spd_mode:
            enable_motor_mode(motor->id, SPD_MODE);
            break;
        case psi_mode:
            enable_motor_mode(motor->id, PSI_MODE);
            break;
        default:
            break;
    }
}

// 电机关闭（禁用模式，并清零设定值）
void dm_motor_disable(motor_t *motor)
{
    switch (motor->ctrl.mode) {
        case mit_mode:
            disable_motor_mode(motor->id, MIT_MODE);
            break;
        case pos_mode:
            disable_motor_mode(motor->id, POS_MODE);
            break;
        case spd_mode:
            disable_motor_mode(motor->id, SPD_MODE);
            break;
        case psi_mode:
            disable_motor_mode(motor->id, PSI_MODE);
            break;
        default:
            break;
    }
    dm_motor_clear_para(motor);
}

// 清除控制设定值
void dm_motor_clear_para(motor_t *motor)
{
    motor->ctrl.kd_set  = 0;
    motor->ctrl.kp_set  = 0;
    motor->ctrl.pos_set = 0;
    motor->ctrl.vel_set = 0;
    motor->ctrl.tor_set = 0;
    motor->ctrl.cur_set = 0;
}

// 清除电机错误（根据模式发送清除命令）
void dm_motor_clear_err(motor_t *motor)
{
    switch (motor->ctrl.mode) {
        case mit_mode:
            clear_err(motor->id, MIT_MODE);
            break;
        case pos_mode:
            clear_err(motor->id, POS_MODE);
            break;
        case spd_mode:
            clear_err(motor->id, SPD_MODE);
            break;
        case psi_mode:
            clear_err(motor->id, PSI_MODE);
            break;
        default:
            break;
    }
}
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

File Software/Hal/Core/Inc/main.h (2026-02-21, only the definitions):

#define LED2_Pin GPIO_PIN_0
#define LED2_GPIO_Port GPIOA
#define LED1_Pin GPIO_PIN_1
#define LED1_GPIO_Port GPIOA
#define KEY1_Pin GPIO_PIN_15
#define KEY1_GPIO_Port GPIOA
#define KEY2_Pin GPIO_PIN_3
#define KEY2_GPIO_Port GPIOB
#define KEY3_Pin GPIO_PIN_4
#define KEY3_GPIO_Port GPIOB
#define KEY4_Pin GPIO_PIN_5
#define KEY4_GPIO_Port GPIOB
#define LED4_Pin GPIO_PIN_8
#define LED4_GPIO_Port GPIOB
#define LED3_Pin GPIO_PIN_9
#define LED3_GPIO_Port GPIOB

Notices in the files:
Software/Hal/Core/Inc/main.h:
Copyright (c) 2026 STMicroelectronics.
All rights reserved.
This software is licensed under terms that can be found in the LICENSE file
